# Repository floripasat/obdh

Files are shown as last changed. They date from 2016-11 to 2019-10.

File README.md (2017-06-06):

# OBDH
On-Board Data Handling module of the FloripaSat Cubesat Project

The main goal of On Board Data Handling, a.k.a. OBDH, is manage all the cubesat information aimming to reach the mission goal.

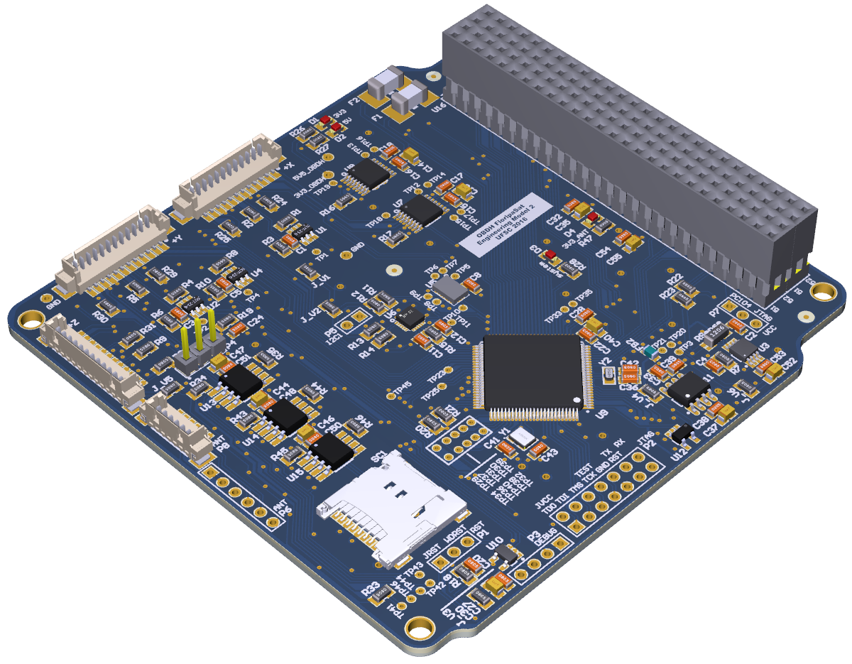
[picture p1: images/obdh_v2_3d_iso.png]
OBDH 3D ISO

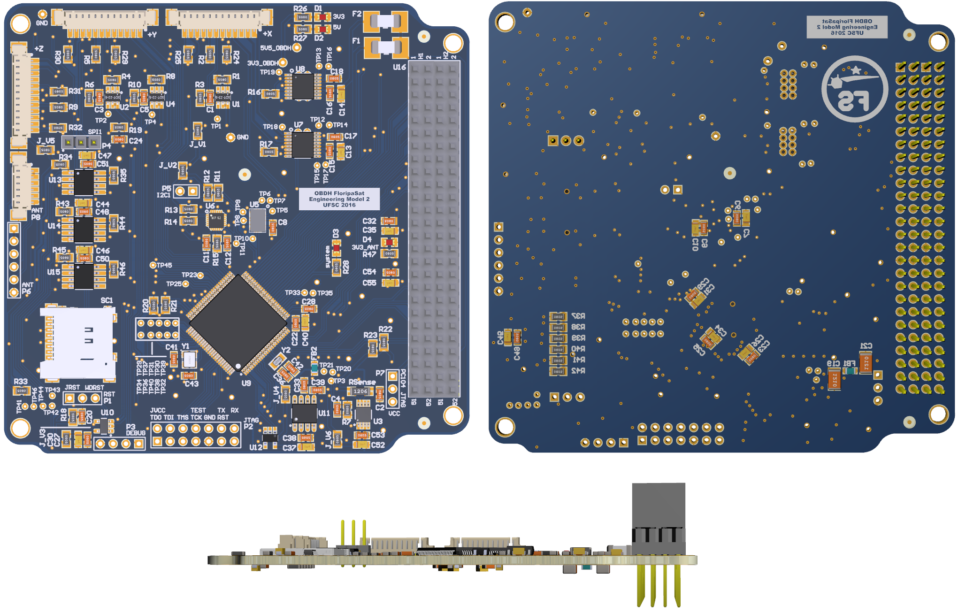
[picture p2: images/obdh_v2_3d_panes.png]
OBDH 3D Panes


## Hardware

* The MCU used in this module is the [MSP430F6659](http://www.ti.com/product/MSP430F6659);
* The tracking IC used is [MPU9250](https://www.invensense.com/products/motion-tracking/9-axis/mpu-9250/), which contains a 9-axis sensors (3-axis each): a gyroscope, an accelerometer and a compass;
* For space-ground communications, is used the radio transceiver [CC1125](http://www.ti.com/product/CC1125);
* Detailed information can be found [here](https://github.com/floripasat/obdh/hardware/).

## Software

* The programming language is C;
* All software was developed in the [Code Composer Studio IDE](http://www.ti.com/tool/ccstudio).
* Tested in compiler TI v16.9.1 LTS (CCS v7.1 7.1.0.00015).
* Uses FreeRTOS, a RTOS for embedded systems. [FreeRTOS page](http://freertos.org/);
* Detailed information can be found [here](https://github.com/floripasat/obdh/firmware/).
<!-- * Doxygen documentation [here](http://fsat-server.duckdns.org:8000/obdh/). nao foi feito ainda -->

### Toolchain setup
* Download and install Code Composer Studio: http://processors.wiki.ti.com/index.php/Download_CCS
* Instructions for for Linux enviroment: http://processors.wiki.ti.com/index.php/Linux_Host_Support_CCSv7
* Select package: MSP430 Ultra Low Power MCUs 
* After installed, open and update CCSv7: Help->Check for Updates->Select All-> Update.. / Restart
* Get the source code: `git clone https://github.com/floripasat/obdh`
* Add the project compiler version: CCS->Help->Install New Software->Work with: All available sites->Disable 'Show only latest version'->Check TI Compoler Updates: MSP430 Compiler Tools 16.6.0 ->Finish/Install/Restart
* Import source project into CCSv7: File->Import->Code Composer Studio->CCS Projects; Select the source folder: obdh/firmware; Leave 'Copy projects into workspace' unchecked.
## References

The general documentation of the project can be found in [GitBook](https://www.gitbook.com/book/tuliogomesp/floripasat-technical-manual).

All source code of the project can be found in [GitHub](https://github.com/floripasat).

The official website of the project is [www.floripasat.ufsc.br](http://www.floripasat.ufsc.br/).

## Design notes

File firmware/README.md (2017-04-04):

# FloripaSat - On Board Data Handling - Software

## FreeRTOS

* Language: C
* The MCU used in this module is the [MSP430F6659](http://www.ti.com/product/MSP430F6659).
* As transceiver, the [CC1125](http://www.ti.com/product/CC1125) IC is used.
* All MCU peripherals are controlled with the ["MSP Driver Library"](http://www.ti.com/tool/mspdriverlib) library, also know as ["DriverLib"](http://www.ti.com/tool/mspdriverlib).
* All software was developed in the [Code Composer Studio IDE](http://www.ti.com/tool/ccstudio) (version 7.1.0.00015), a.k.a. CCS. The compiler used is TI MSP430 Compiler, version 16.9.1 LTS).

## Software flow

1. Antenna Deployment Countdown 
2. Antenna Deployment
3. Watchdog timer configuration
4. Peripherals initialization 
5. Start tasks

## USCI Configuration

| MSP INTERFACE | MODE | CONNECTED COMPONENTS |
|:---|:---|:---|
| USCI_A0 | SPI | TRANSCEIVER |
| USCI_A1 | SPI | MAIN BUS (flash/SD memory, ADC1, ADC2, ADC3, ADCS) |
| USCI_A2 | UART | DEBUG |
| USCI_B0 | I2C | EPS (EPS as slave) |
| USCI_B1 | I2C | MAIN BUS (IMU1, IMU2) |
| USCI_B2 | I2C | ANTENNA DEPLOYMENT |

## Debug mode

The Debug mode was used to print log messages.

The debug mode can be used with a UART-USB converter (FTDI chip for example) with the follow configuration:
* Baudrate = 9600 bps
* Data bits = 8
* Parity bit = None
* Stop bits = 1

## References

The general documentation of the project can be found in [GitBook](https://www.gitbook.com/book/tuliogomesp/floripasat-technical-manual).

All source code of the project can be found in [GitHub](https://github.com/floripasat/).

The official website of the project is [www.floripasat.ufsc.br](http://www.floripasat.ufsc.br/).

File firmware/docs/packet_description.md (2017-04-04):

# Packet Description

Esse documento deve seguir as informações contidas em: https://docs.google.com/spreadsheets/d/1e5KTyQqeFW5pgzqara0UhxRcPHhF5Oq5QgL1BtvwexI

## Package flags

### Length (bytes)
2

### Description

Contém 1 bit flag para cada um dos submódulos seguintes do pacote. Se o bit estiver setado, significa que o pacote contém dados daquele determinado módulo. Durante a persistência de dados em memória não-volátil, uma flag zerada significa que os dados do submódulo referido serão armazenados com o valor 0 e podem ser ignorados no pacote, porém mantendo o pacote de tamanho fixo. Já durante um envio de dados para o segmento terrestre, uma flag zerada significa que o pacote não contém aquela seção de dados referente ao submódulo, fazendo com que o tamanho total do pacote seja menor.

## System status

### Length (bytes)
5

### Description

Contém um contador de resets (3 bytes) e flags que sinalizam quais submódulos estão funcionando (2 bytes). 

## IMU

### Length (bytes)
20

### Description
Inercial Measure Unit data.

3-axis accelerometer - 6 bytes
<p><strong>Cálculo:</strong>   (((HIGH_BYTE << 8 | LOW_BYTE) * IMU_ACC_RANGE) / 32768.0) , onde IMU_ACC_RANGE depende da sensibilidade configurada (2g a 16g).</p>

3-axis gyroscope - 6 bytes
<p><strong>Cálculo:</strong>   (((HIGH_BYTE << 8 | LOW_BYTE) * IMU_GYRO_RANGE) / 32768.0) , onde IMU_GYRO_RANGE depende da sensibilidade configurada (250º/s a 2000º/s).</p>

3-axis magnetometer - 6 bytes

temperature - 2 bytes

<p><strong>Cálculo:</strong>   (((HIGH_BYTE << 8 | LOW_BYTE) / IMU_TEMP_RANGE ) + 21), onde IMU_TEMP_RANGE = 500.</p>

## MSP Sensors

### Length (bytes)
6
### Description

MSP internal temperature sensor (2 bytes)

<p><strong>Cálculo:</strong>   ((HIGH_BYTE << 8 | LOW_BYTE) * 2 - COEF_30C) * 55) / (COEF_85C - COEF_30C) + 30, onde COEF_XX é o coeficiente de calibraçao salvo na memoria flash do MSP.</p>

Supply voltage (2 bytes)

<p><strong>Cálculo:</strong>    (HIGH_BYTE << 8 | LOW_BYTE) * AVCC * VOLTAGE_DIVISOR / ADC_RANGE, onde AVCC = 3.3, VOLTAGE_DIVISOR = 2, ADC_RANGE = 3.</p>

Supply current (2 bytes)
<p><strong>Cálculo:</strong>    (HIGH_BYTE << 8 | LOW_BYTE) * (AVCC / (ADC_RANGE * RL_VALUE * CURRENT_GAIN * RSENSE_VALUE), onde AVCC = 3.3, ADC_RANGE = 3, RL_VALUE = 0.05, CURRENT_GAIN = 0.025 e RSENSE_VALUE = 20000.</p>

## Systick

### Length (bytes)
4

### Description
Tempo desde o último reset, em milisegundos.

## Solar Panels

### Length (bytes)
42

### Description
3 solar panels has 1-axis accelerometer, gyroscope and magnetometer (2 bytes each axis each panel). Every panels has a sun sensor and a temperature sensor (2 bytes each). (2+2+2) * 3 + (2+2) * 6 = 42 bytes.

## RTC

### Length (bytes)
8

### Description
Seconds, minutes, hours, day of week, day of month, month (1 byte each) and year (2 bytes).

## Radio

### Length (bytes)
100

### Description
RSSI do rádio (2 bytes)
Últimos comandos recebidos

## ADC Solar Panels

### Length (bytes)
18

### Description
ADC solar panel current - 12 bytes
ADC solar panel voltage - 6 bytes

## MSP430 ADC

### Length (bytes)
8

### Description
ADC total voltage - 2 bytes 
ADC bus voltage - 2 bytes
ADC beacon/eps current - 2 bytes
ADC internal temperature sensor - 2 bytes

## Battery Monitor

### Length (bytes)
21

### Description
Battery average current - 2 bytes
Battery monitor temperature - 2 bytes
Battery voltage - 4 bytes
Battery current - 2 bytes
Battery accumulated current - 2 bytes
Protection register - 1 byte
Status register - 1 byte
Cycle counter register - 1 byte
Remaining active absolute capacity register - 2 bytes
Remaining standby absolute capacity register - 2 bytes
Remaining active relative capacity - 1 byte
Remaining standby relative capacity - 1 byte

## ADS1248

### Length (bytes)
21

### Description
7 RTDs measurements via ADS1248 - 21 bytes

## Task Scheduler

### Length (bytes)
1

### Description
EPS status - 1 byte

## Beacon

### Length (bytes)
3

### Description
Radio temperature - 1 byte
Transmitted power - 1 byte
DAC voltage (power amplifier control) - 1 byte

## Transceiver

### Length (bytes)
4

### Description
Radio temperature - 1 byte
Received signal power - 1 byte
Transmitted power - 1 byte
DAC voltage (power amplifier control) - 1 byte

## Payload1

### Length (bytes)
7

### Description
Voltage on the thermoeletric generator with/without load and energy stored on the last 3 minutes (7 bytes total)

## Payload2

### Length (bytes)
100

### Description
Single Event Upset Detection

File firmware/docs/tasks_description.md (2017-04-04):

# Tasks Description

## wdt_task

#### Descrição

Esta tarefa irá resetar os dois watchdog timers (interno e externo) a cada execução. No modo DEBUG ela também faz o system_led piscar para termos um recurso visual no momento da depuração.

#### Dados gerados

Nenhum

#### Período da tarefa

500 ms.

#### Prioridade

5

#### Recursos utilizados

GPIO WDI_EXT;
GPIO LED_SYSTEM.

## store_data_task

#### Descrição

Esta tarefa recebe, por meio de filas de mensagens, os dados de outras tarefas, os quais deve salvar em uma memória não-volátil. Os dados são salvos em blocos de 512 bytes. Os dados são armazenados conforme a tabela: https://docs.google.com/spreadsheets/d/1e5KTyQqeFW5pgzqara0UhxRcPHhF5Oq5QgL1BtvwexI. 

O esquema de armazenamento dá-se da seguinte forma: se houver mensagens (novos dados) na fila de mensagens referente a determinado submódulo, sua respectiva flag é setada no pacote e os dados salvos na memória. Os submódulos que não possuírem novas mensagens são zerados no pacote, juntamente com sua flag, e ambos salvos na memória (com valor 0). No momento da leitura do pacotes salvos em memória, as flags irão indicar quais submódulos contém dados válidos e quais devem ser ignorados. Isso faz com que as transmissões de dados enviem somente informações relevantes, economizando banda de transmissão.

#### Dados gerados

Não se aplica

#### Período da tarefa

Depende das demais tarefas: ela deve ter período menor ou igual ao menor período das outras tarefas, de maneira a não perder nenhuma leitura.

#### Prioridade

5

#### Recursos utilizados

GPIO uSDCard_CE;
GPIO Mem_WP;
GPIO Mem0_CE;
GPIO Mem1_CE;
GPIO Mem2_CE;
GPIO Mem2_CE;
GPIO Mem2_CE;
SPI 1 (USCI A1).

## communications_task

#### Descrição

Esta tarefa controla o Link de comunicação (uplink e downlink). Ela irá aguardar a recpeção de mensagens pelo rádio (uplink) e, eventualmente, responderá aos comandos recebidos. Alguns comandos são:
- Shutdown all communications over 24 hours;
- Send data (com as especificações dos dados desejados).

#### Dados gerados

RSSI do rádio
Últimos comandos recebidos

#### Período da tarefa

100ms

#### Prioridade

5

#### Recursos utilizados

GPIO TTC_GPIO0_MAIN;
GPIO TTC_GPIO2_MAIN;
GPIO TTC_RESETn_MAIN;
GPIO TTC_CTRL_RF_SWT_TX;
GPIO TTC_CTRL_RF_SWT_RX;
GPIO Mem2_CE;
GPIO Mem2_CE;
SPI 0 (USCI A0);
GPIO uC_BEACON_0;
GPIO uC_BEACON_1;
GPIO uC_BEACON_2;
GPIO uC_BEACON_3.

## read_internal_sensors_task

#### Descrição

Esta tarefa faz a leitura do sensor de temperatura interno do MSP, da tensão e da corrente de alimentação. Estes valores são enviados por meio de uma fila de mensagens para a tarefa store_data.

#### Dados gerados

Internal temperature (2 bytes)
Supply voltage (2 bytes)
Supply current (2 bytes)
TOTAL = 6 bytes

#### Período da tarefa

1000ms

#### Prioridade

1

#### Recursos utilizados

GPIO OBDH_CURRENT_ADC;
GPIO ADC_VCC_3V3;
ADC.

## imu_interface_task

#### Descrição

Esta tarefa faz a leitura dos sensores que compõem a IMU (Inertial Measure Unit). Estes são: acelerômetro, giroscópio e magnetômetro, em 3 eixos, e um sensor de temperatura. 

#### Dados gerados

Accelerometer axis X(2 bytes)
Accelerometer axis Y(2 bytes)
Accelerometer axis Z(2 bytes)
Gyroscope axis X(2 bytes)
Gyroscope axis Y(2 bytes)
Gyroscope axis Z(2 bytes)
Magnetometer axis X(2 bytes)
Magnetometer axis Y(2 bytes)
Magnetometer axis Z(2 bytes)
Temperature sensor(2 bytes)
TOTAL = 20 bytes

#### Período da tarefa

10.000ms

#### Prioridade

1

#### Recursos utilizados

I2C 1.

## debug_task

#### Descrição

Esta tarefa somente é criada quando o build está em modo "DEBUG". Ela imprime mensagens, via UART, 

#### Dados gerados

Internal temperature (2 bytes)
Supply voltage (2 bytes)
Supply current (2 bytes)
TOTAL = 6 bytes

#### Período da tarefa

1000ms

#### Prioridade

1

#### Recursos utilizados

GPIO OBDH_CURRENT_ADC;
GPIO ADC_VCC_3V3;
ADC.

## imu_interface_task

#### Descrição

Esta tarefa faz a leitura dos sensores que compõem a IMU (Inertial Measure Unit). Estes são: acelerômetro, giroscópio e magnetômetro, em 3 eixos, e um sensor de temperatura. 

#### Dados gerados

Accelerometer axis X(2 bytes)
Accelerometer axis Y(2 bytes)
Accelerometer axis Z(2 bytes)
Gyroscope axis X(2 bytes)
Gyroscope axis Y(2 bytes)
Gyroscope axis Z(2 bytes)
Magnetometer axis X(2 bytes)
Magnetometer axis Y(2 bytes)
Magnetometer axis Z(2 bytes)
Temperature sensor(2 bytes)
TOTAL = 20 bytes

#### Período da tarefa

10.000ms

#### Prioridade

1

#### Recursos utilizados

I2C 1.

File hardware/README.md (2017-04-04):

# FloripaSat - On Board Data Handling - Hardware
<hr>
## Topology

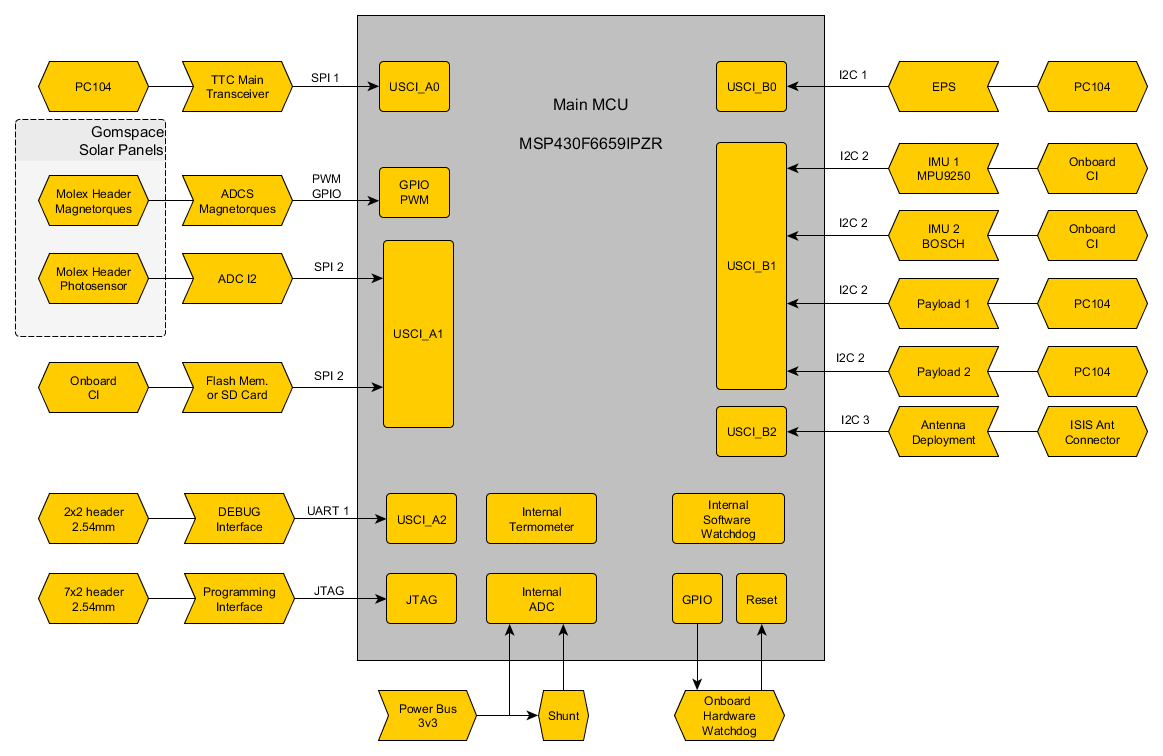
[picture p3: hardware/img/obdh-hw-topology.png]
Topology
  

<hr>

## Pin Assignaments

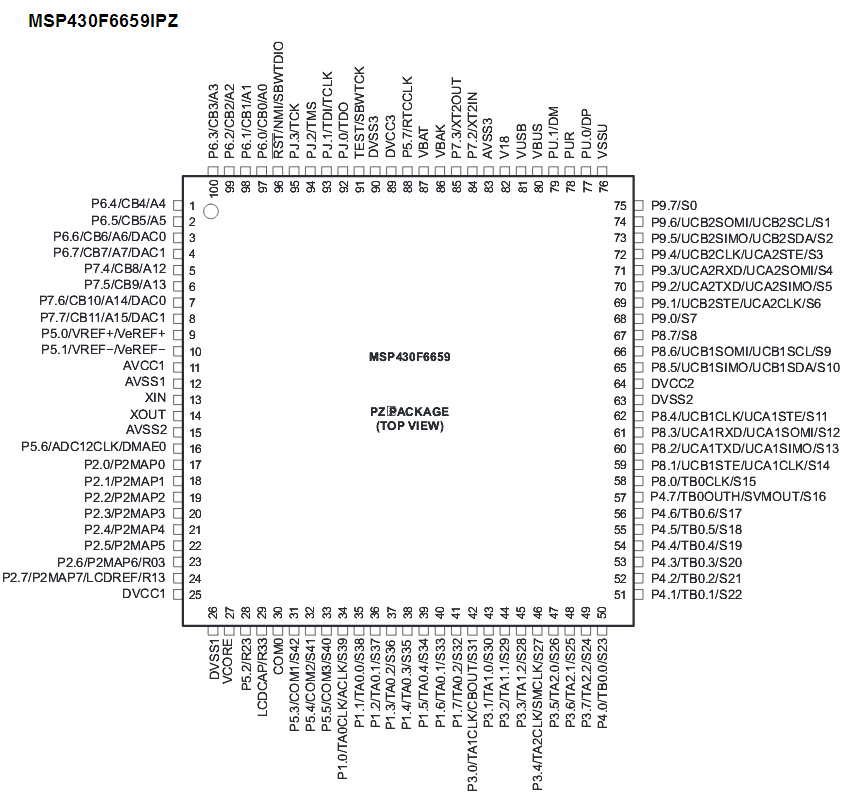
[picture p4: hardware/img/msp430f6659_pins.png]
Pin Designation
  

| PIN  NUMBER | PIN  NAME | OBDH  NAME |
|:--|:---|:---|
|1  |P6.4/CB4/A4 ||
|2  |P6.5/CB5/A5 ||
|3  |P6.6/CB6/A6/DAC0 ||
|4  |P6.7/CB7/A7/DAC1 ||
|5  |P7.4/CB8/A12 ||
|6  |P7.5/CB9/A13 ||
|7  |P7.6/CB10/A14/DAC0 ||
|8  |P7.7/CB11/A15/DAC1 ||
|9  |P5.0/VREF+/VeREF+ ||
|10 |P5.1/VREF-/VeREF- ||
|11 |AVCC1 ||
|12 |AVSS1 ||
|13 |XIN ||
|14 |XOUT ||
|15 |AVSS2 ||
|16 |P5.6/ADC12CLK/DMAE0 ||
|17 |P2.0/P2MAP0 ||
|18 |P2.1/P2MAP1 ||
|19 |P2.2/P2MAP2 ||
|20 |P2.3/P2MAP3 ||
|21 |P2.4/P2MAP4 ||
|22 |P2.5/P2MAP5 ||
|23 |P2.6/P2MAP6/R03 ||
|24 |P2.7/P2MAP7/LCDREF/R13 ||
|25 |DVCC1 ||
|26 |DVSS1 ||
|27 |VCORE ||
|28 |P5.2/R23 ||
|29 |LCDCAP/R33 ||
|30 |COM0 ||
|31 |P5.3/COM1/S42 ||
|32 |P5.4/COM2/S41 ||
|33 |P5.5/COM3/S40 ||
|34 |P1.0/TA0CLK/ACLK/S39 ||
|35 |P1.1/TA0.0/S38 ||
|36 |P1.2/TA0.1/S37 ||
|37 |P1.3/TA0.2/S36 ||
|38 |P1.4/TA0.3/S35 ||
|39 |P1.5/TA0.4/S34 ||
|40 |P1.6/TA0.1/S33 ||
|41 |P1.7/TA0.2/S32 ||
|42 |P3.0/TA1CLK/CBOUT/S31 ||
|43 |P3.1/TA1.0/S30 ||
|44 |P3.2/TA1.1/S29 ||
|45 |P3.3/TA1.2/S28 ||
|46 |P3.4/TA2CLK/SMCLK/S27 ||
|47 |P3.5/TA2.0/S26 ||
|48 |P3.6/TA2.1/S25 ||
|49 |P3.7/TA2.2/S24 ||
|50 |P4.0/TB0.0/S23 ||
|51 |P4.1/TB0.1/S22 ||
|52 |P4.2/TB0.2/S21 ||
|53 |P4.3/TB0.3/S20 ||
|54 |P4.4/TB0.4/S19 ||
|55 |P4.5/TB0.5/S18 ||
|56 |P4.6/TB0.6/S17 ||
|57 |P4.7/TB0OUTH/SVMOUT/S16  ||
|58 |P8.0/TB0CLK/S15 ||
|59 |P8.1/UCB1STE/UCA1CLK/S14 ||
|60 |P8.2/UCA1TXD/UCA1SIMO/S13||
|61 |P8.3/UCA1RXD/UCA1SOMI/S12||
|62 |P8.4/UCB1CLK/UCA1STE/S11 ||
|63 |DVSS2 ||
|64 |DVCC2 ||
|65 |P8.5/UCB1SIMO/UCB1SDA/S10||
|66 |P8.6/UCB1SOMI/UCB1SCL/S9 ||
|67 |P8.7/S8 ||
|68 |P9.0/S7 ||
|69 |P9.1/UCB2STE/UCA2CLK/S6  ||
|70 |P9.2/UCA2TXD/UCA2SIMO/S5 ||
|71 |P9.3/UCA2RXD/UCA2SOMI/S4 ||
|72 |P9.4/UCB2CLK/UCA2STE/S3  ||
|73 |P9.5/UCB2SIMO/UCB2SDA/S2 ||
|74 |P9.6/UCB2SOMI/UCB2SCL/S1 ||
|75 |P9.7/S0 ||
|76 |VSSU ||
|77 |PU.0/DP ||
|78 |PUR ||
|79 |PU.1/DM ||
|80 |LDOI ||
|81 |VUSB ||
|82 |V18 ||
|83 |AVSS3 ||
|84 |P7.2/XT2IN ||
|85 |P7.3/XT2OUT ||
|86 |VBAK ||
|87 |VBAT ||
|88 |P5.7/RTCCLK ||
|89 |DVCC3 ||
|90 |DVSS3 ||
|91 |TEST/SBWTCK ||
|92 |PJ.0/TDO ||
|93 |PJ.1/TDI/TCLK ||
|94 |PJ.2/TMS ||
|95 |PJ.3/TCK ||
|96 |RST/NMI/SBWTDIO ||
|97 |P6.0/CB0/A0 ||
|98 |P6.1/CB1/A1 ||
|99 |P6.2/CB2/A2 ||
|100|P6.3/CB3/A3 ||
<hr>

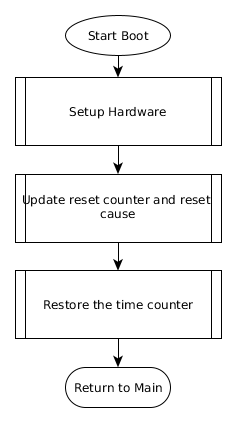
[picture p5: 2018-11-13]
images/flowcharts/boot_flowchart.png

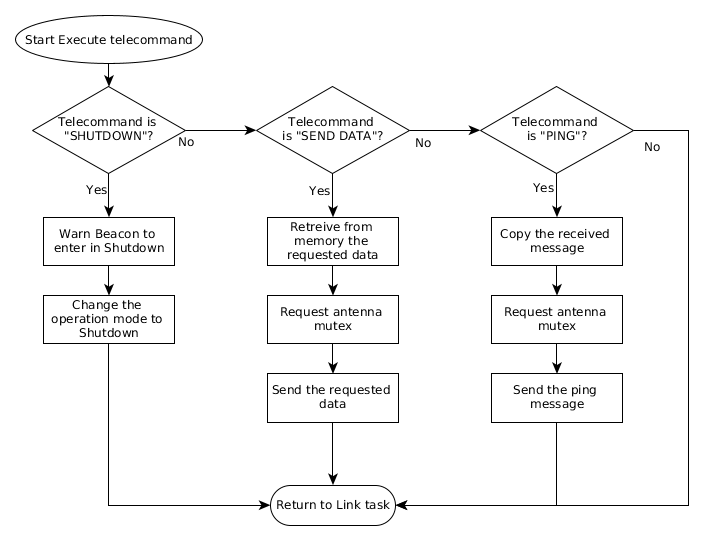
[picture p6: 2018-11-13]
images/flowcharts/execute_telecommand_flowchart.png

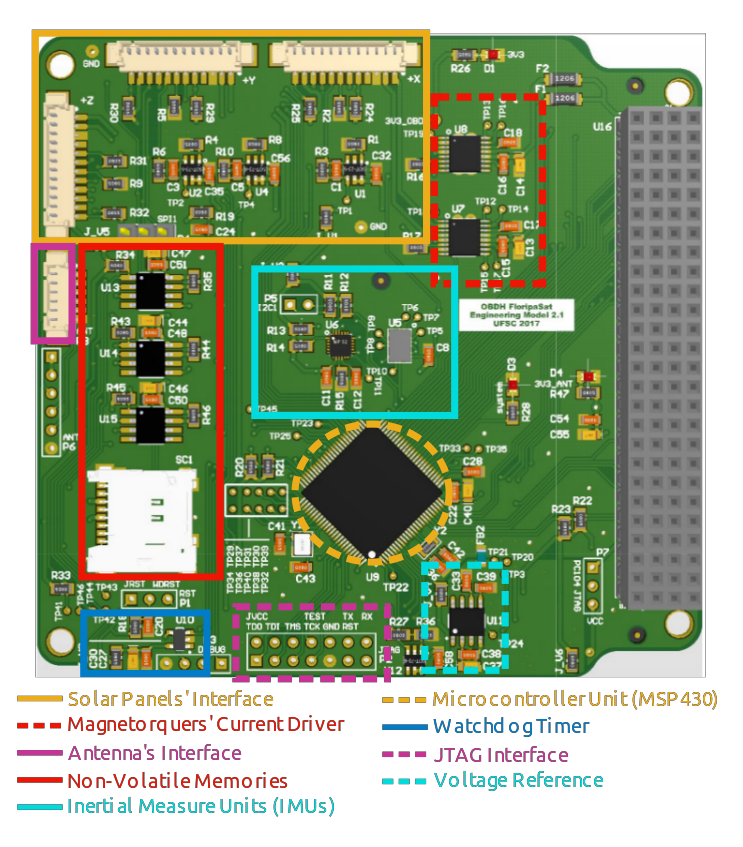
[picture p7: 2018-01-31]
images/obdh-hw-submodules.png

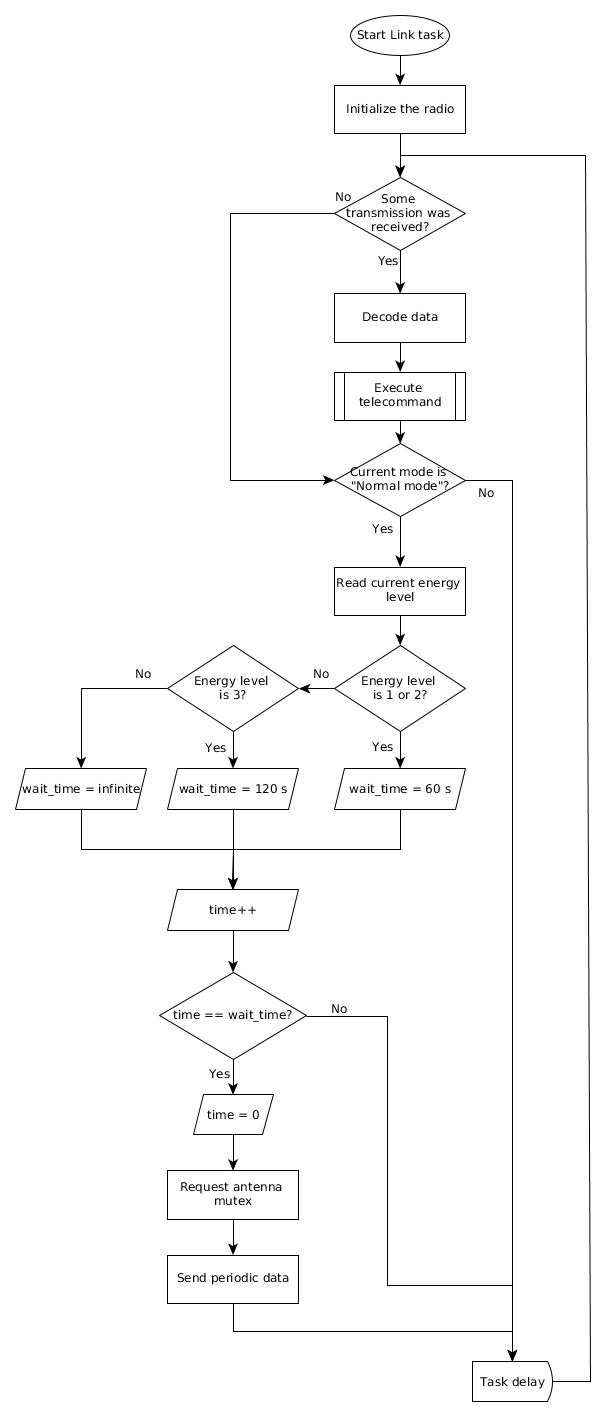
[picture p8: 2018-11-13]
images/flowcharts/link_task_flowchart.png

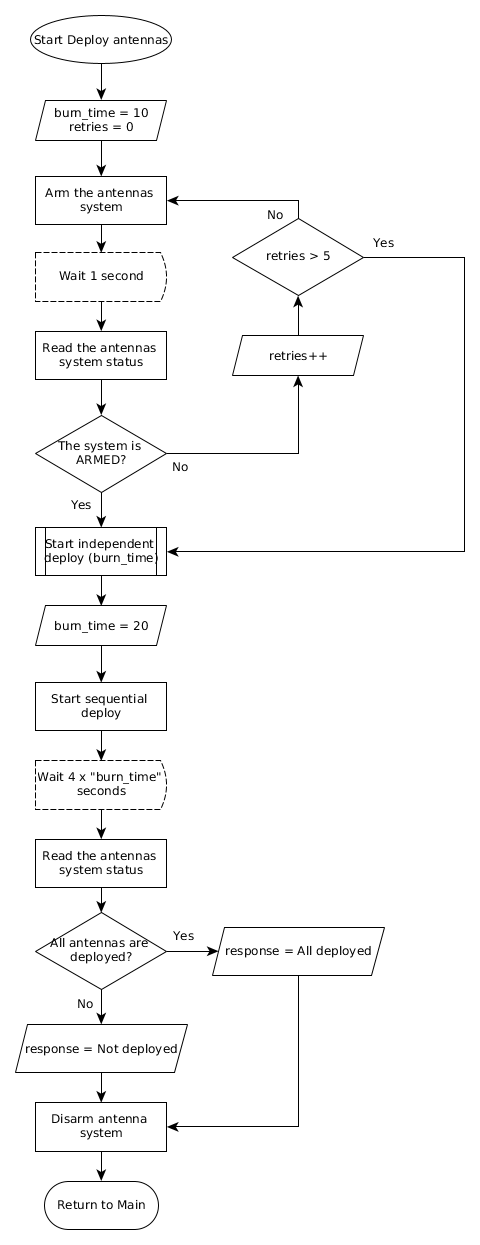
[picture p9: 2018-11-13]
images/flowcharts/deploy_antennas_flowchart.png

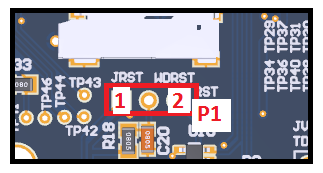
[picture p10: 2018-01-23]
images/obdh_jumper_reset_source.png

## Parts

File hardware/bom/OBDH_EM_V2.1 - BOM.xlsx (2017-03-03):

Mount | Designator | Manufacter PartNumber | Digikey Part Number | Description | Qtd | Price per unit(USD) | Total
TRUE | C13, C14 | TPSP106M010R2000 | 511-1685-1-ND (http://www.digikey.com/product-detail/en/rohm-semiconductor/TCP1A106M8R/511-1685-1-ND/4571361) | 10µF Molded Tantalum Capacitors 10V | 2 | $0.60 | $1.20
TRUE | C7, C10, C26, C30, C31, C34, C37, C40, C44, C45, C46, C47, C52, C55 | F920J106MPA | 478-8115-1-ND (http://www.digikey.com/product-detail/en/avx-corporation/F920J106MPA/478-8115-1-ND/4005541) | 10µF Molded Tantalum Cap 6.3V 0805 | 14 | $0.22 | $3.05
TRUE | C17, C18 | C2012X7R1C225K125AB | 445-1420-1-ND (http://www.digikey.com/product-detail/en/tdk-corporation/C2012X7R1C225K125AB/445-1420-1-ND/569086) | 2.2µF 16V Ceramic Capacitor X7R 0805 | 2 | $0.20 | $0.40
TRUE | C19, C21 | C3225X7R1C226K250AC | 445-3945-1-ND (http://www.digikey.com/product-detail/en/tdk-corporation/C3225X7R1C226K250AC/445-3945-1-ND/1944441) | 22µF 16V Ceramic Capacitor X7R 1210 | 2 | $0.85 | $1.70
TRUE | C36, C42 | CL21C120FBANNNC | 1276-2579-1-ND (http://www.digikey.com/product-detail/en/samsung-electro-mechanics-america-inc/CL21C120FBANNNC/1276-2579-1-ND/3890665) | 12pF 50V Ceramic Capacitor C0G, NP0 0805 | 2 | $0.13 | $0.26
TRUE | C11, C15, C16, C39 | CL21B103KAANNNC | 1276-2434-1-ND (http://www.digikey.com/product-detail/en/samsung-electro-mechanics-america-inc/CL21B103KAANNNC/1276-2434-1-ND/3890520) | CAP CER 0.01uF 25V 10% X7R 0805 | 4 | $0.10 | $0.40
TRUE | C28 | C0805C474K5RACTU | 399-8100-1-ND (http://www.digikey.com/product-detail/en/kemet/C0805C474K5RACTU/399-8100-1-ND/3471823) | 0.47µF 50V Ceramic Capacitor X7R 0805 | 1 | $0.25 | $0.25
FALSE | C24 | CGA4J2C0G1H223J125AA | 445-6949-1-ND (http://www.digikey.com/product-detail/en/tdk-corporation/CGA4J2C0G1H223J125AA/445-6949-1-ND/2672967) | 0.022µF ±5% 50V Ceramic Capacitor C0G, NP0 0805 | 1 | $0.32 | $0.32
TRUE | C20 | C0805C473J3GACTU | 399-8092-1-ND (http://www.digikey.com/product-detail/en/kemet/C0805C473J3GACTU/399-8092-1-ND/3471815) | 0.047µF 25V Ceramic Capacitor C0G, NP0 0805 | 1 | $0.72 | $0.72
TRUE | C1, C3, C5 | CC0805JRNPO9BN180 | 311-1102-1-ND (http://www.digikey.com/product-detail/en/yageo/CC0805JRNPO9BN180/311-1102-1-ND/303012) | 18pF 50V Ceramic Capacitor C0G, NP0 0805 | 3 | $0.10 | $0.30
TRUE | C2, C4, C6, C8, C9, C12, C22, C23, C25, C27, C29, C32, C33, C35, C38, C48, C49, C50, C51, C53, C54, C56, C58 | CC0805KRX7R8BB104 | 311-1141-1-ND (http://www.digikey.com/product-detail/en/yageo/CC0805KRX7R8BB104/311-1141-1-ND/303051) | CAP CER 0.1UF 25V 10% X7R 0805 | 23 | $0.05 | $1.15
FALSE | C41, C43 | 08051A100FAT2A | 478-5779-1-ND (http://www.digikey.com/product-detail/en/avx-corporation/08051A100FAT2A/478-5779-1-ND/2136371) | 10pF 100V Ceramic Capacitor C0G, NP0 0805 | 2 | $0.46 | $0.92
TRUE | J_V1, J_V2, J_V3, J_V4, J_V5, J_V6, R1, R2, R4, R5, R8, R9, R13, R14, R15 | RC0805JR-070RL | 311-0.0ARCT-ND (http://www.digikey.com/product-detail/en/yageo/RC0805JR-070RL/311-0.0ARCT-ND/731163) | RES SMD 0.0 OHM JUMPER 1/8W 0805 | 17 | $0.02 | $0.31
TRUE | R11, R12, R20, R21, R22, R23, R24, R25, R29, R30, R31, R32, R33, R34, R35, R43, R44, R45, R46 | CRCW080510K0FKEA | 541-10.0KCCT-ND (http://www.digikey.com/product-detail/en/vishay-dale/CRCW080510K0FKEA/541-10.0KCCT-ND/1180897) | RES 10K OHM 1/8W 1% 0805 | 19 | $0.04 | $0.76
FALSE | R37, R38, R39, R40, R41, R42 | CRCW080510K0FKEA | 541-10.0KCCT-ND (http://www.digikey.com/product-detail/en/vishay-dale/CRCW080510K0FKEA/541-10.0KCCT-ND/1180897) | RES 10K OHM 1/8W 1% 0805 | 6 | $0.04 | $0.24
TRUE | R7 | PCF0805R-1K65BT1 | 985-1304-1-ND (http://www.digikey.com/product-detail/en/tt-electronics-welwyn/PCF0805R-1K65BT1/985-1304-1-ND/2402146) | RES SMD 1.65KOHM 0.1% 1/10W 0805 | 1 | $0.61 | $0.61
TRUE | R18, R27, R36 | RC0805FR-0747KL | 311-47.0KCRCT-ND (http://www.digikey.com/product-detail/en/yageo/RC0805FR-0747KL/311-47.0KCRCT-ND/730920) | RES SMD 47K OHM 1% 1/8W 0805 | 1 | $0.01 | $0.01
FALSE | R19 | RC0805FR-0733KL | 311-33.0KCRCT-ND (http://www.digikey.com/product-detail/en/yageo/RC0805FR-0733KL/311-33.0KCRCT-ND/730810) | RES SMD 33K OHM 1% 1/8W 0805 | 1 | $0.01 | $0.01
TRUE | R16, R17 | RL1220S-R20-F | RL12S.20FCT-ND (http://www.digikey.com/product-detail/en/susumu/RL1220S-R20-F/RL12S.20FCT-ND/433023) | RES SMD 0.2 OHM 1% 1/3W 0805 | 2 | $0.32 | $0.64
TRUE | R26, R47 | RC0805FR-071KL | 311-1.00KCRCT-ND (http://www.digikey.com/product-detail/en/yageo/RC0805FR-071KL/311-1.00KCRCT-ND/730391) | RES SMD 1K OHM 1% 1/8W 0805 | 2 | $0.01 | $0.02
TRUE | R28 | RC0805FR-07330RL | 311-330CRCT-ND (http://www.digikey.com/product-detail/en/yageo/RC0805FR-07330RL/311-330CRCT-ND/730813) | RES SMD 330 OHM 1% 1/8W 0805 | 1 | $0.01 | $0.01
TRUE | R3, R6, R10 | RC0805FR-073K3L | 311-3.30KCRCT-ND (http://www.digikey.com/product-detail/en/yageo/RC0805FR-073K3L/311-3.30KCRCT-ND/730760) | RES SMD 3.3K OHM 1% 1/8W 0805 | 3 | $0.01 | $0.03
TRUE | RSense | LVK12R050DER | LVK12R050DERCT-ND (http://www.digikey.com/product-detail/en/ohmite/LVK12R050DER/LVK12R050DERCT-ND/1632800) | RES SMD 0.05 OHM 0.5% 1/2W 1206 | 1 | $0.86 | $0.86
TRUE | Y2 | ECS-.327-12.5-34S-TR | XC1967CT-ND (http://www.digikey.com/product-detail/en/ecs-inc/ECS-.327-12.5-34S-TR/XC1967CT-ND/3927391) | 32.768kHz ±20ppm Crystal 12.5pF 70 kOhm -40°C ~ 125°C Surface Mount 2-SMD | 1 | $1.20 | $1.20
TRUE | Y1 | ABM8X-102-32.000MHZ-T | 535-11454-1-ND (http://www.digikey.com/product-detail/en/abracon-llc/ABM8X-102-32.000MHZ-T/535-11454-1-ND/2673402) | 32MHz ±10ppm Crystal 10pF 60 Ohm -40°C ~ 125°C Surface Mount 4-SMD | 1 | $6.18 | $6.18
TRUE | D1, D4 | LTST-C171GKT | 160-1423-1-ND (http://www.digikey.com/product-detail/en/lite-on-inc/LTST-C171GKT/160-1423-1-ND/386792) | Green 569nm LED Indication - Discrete 2.1V 0805 (2012 Metric) | 1 | $0.29 | $0.29
TRUE | D3 | LTST-C170KFKT | 160-1413-1-ND (http://www.digikey.com/product-detail/en/lite-on-inc/LTST-C170KFKT/160-1413-1-ND/386774) | Orange 605nm LED Indication - Discrete 2V 0805 (2012 Metric) | 1 | $0.29 | $0.29
TRUE | F1, F2 | 0437.375WR | F2878CT-ND (http://www.digikey.com/product-detail/en/littelfuse-inc/0437.375WR/F2878CT-ND/1905893) | FUSE BOARD MNT 375MA 125VAC/VDC | 2 | $0.96 | $1.92
TRUE | FB1, FB2 | BLM21PG300SN1D | 490-1052-1-ND (http://www.digikey.com/product-detail/en/murata-electronics-north-america/BLM21PG300SN1D/490-1052-1-ND/584499) | FERRITE BEAD 30 OHM 0805 1LN | 2 | $0.12 | $0.24
TRUE | U6 | MPU-9250 | 1428-1019-1-ND (http://www.digikey.com/product-search/en?keywords=1428-1019-1-ND) | GYRO/ACCEL/COMPASS/9-AXIS | 1 | $10.64 | $10.64
TRUE | U5 | BMX055 | 828-1060-1-ND (http://www.digikey.com/product-detail/en/bosch-sensortec/BMX055/828-1060-1-ND/6136311) | Bosch Adx/Gyro/Magneto 3 axis | 1 | $7.99 | $7.99
TRUE | U1, U2, U4, U12 | TLV341AIDBVR | 296-17680-1-ND (http://www.digikey.com/product-detail/en/texas-instruments/TLV341AIDBVR/296-17680-1-ND/716532) | General Purpose Amplifier 1 Circuit Rail-to-Rail SOT-23-6 | 4 | $1.09 | $4.36
TRUE | U13, U14, U15 | IS25LP128-JBLE | 706-1341-ND (http://www.digikey.com/product-detail/en/issi-integrated-silicon-solution-inc/IS25LP128-JBLE/706-1341-ND/5189776) | IC FLASH 128MBIT 133MHZ 8SOIC | 3 | $2.21 | $6.63
TRUE | U7, U8 | DRV8833PWPR | 296-29434-1-ND (http://www.digikey.com/product-detail/en/texas-instruments/DRV8833PWPR/296-29434-1-ND/2743171) | IC MOTOR DRIVER PAR 16HTSSOP | 2 | $2.46 | $4.92
TRUE | U9 | MSP430F6659IPZ | 296-41521-ND (http://www.digikey.com/product-detail/en/texas-instruments/MSP430F6659IPZ/296-41521-ND/3902666) | 16-bit Microcontrollers - MCU Mixed Signal MCU | 1 | $12.25 | $12.25
TRUE | U10 | TPS3823-33QDBVRQ1 | 296-15650-1-ND (http://www.digikey.com/product-detail/en/texas-instruments/TPS3823-33QDBVRQ1/296-15650-1-ND/2057470) | IC SUPERVISORY CIRCUIT SOT23-5 | 1 | $1.73 | $1.73
TRUE | U3 | MAX9934TAUA+ | MAX9934FAUA+-ND (http://www.digikey.com/product-detail/en/maxim-integrated/MAX9934FAUA-/MAX9934FAUA--ND/2239126) | Current Sense Amplifier 1 Circuit 8-uMAX | 1 | $1.68 | $1.68
TRUE | U11 | REF5030AQDRQ1 | 296-27911-1-ND (http://www.digikey.com/product-detail/en/texas-instruments/REF5030AQDRQ1/296-27911-1-ND/2428322) | Voltage References Low NoiseVery Low DriftPrec Vltg Ref - 3V | 1 | $3.62 | $3.62
TRUE | SC1 | 5031821852 | WM12834CT-ND (http://www.digikey.com/product-search/en?keywords=WM12834CT-ND) | 9 (8 + 1) Position Card Connector microSD™ Surface Mount, Right Angle Gold | 1 | $2.33 | $2.33
TRUE | +X, +Y, +Z | 0533981271 | WM7616CT-ND (http://www.digikey.com/product-detail/en/molex-llc/0533981271/WM7616CT-ND/699090) | 12 Positions Header, Shrouded Connector 0.049" (1.25mm) Surface Mount Tin | 3 | $2.16 | $6.48
TRUE | U16A, U16B | ESQ-126-39-G-D | SAM8772-ND (http://www.digikey.com/product-detail/en/samtec-inc/ESQ-132-39-G-D/SAM8772-ND/2640989) | CONN RCPT 64POS .100" DUAL GOLD | 2 | $11.08 | $22.16
TRUE | P1, P4, P7 | 961103-6404-AR | 3M9448-ND (http://www.digikey.com/product-detail/en/3m/961103-6404-AR/3M9448-ND/2071489) | CONN HEADER VERT SGL 3POS GOLD | 3 | $0.26 | $0.78
TRUE | P5 | M20-9990246 | 952-2262-ND (http://www.digikey.com/product-detail/en/harwin-inc/M20-9990246/952-2262-ND/3728226) | SIL VERTICAL PC TAIL PIN HEADER | 1 | $0.11 | $0.11
TRUE | P6 | 68000-406HLF | 609-3263-ND (http://www.digikey.com/product-detail/en/amphenol-fci/68000-406HLF/609-3263-ND/1878471) | CONN HEADER 6POS .100 STR TIN | 1 | $0.25 | $0.25
TRUE | P3 | 961104-6404-AR | 3M9449-ND (http://www.digikey.com/product-detail/en/3m/961104-6404-AR/3M9449-ND/2071490) | CONN HEADER VERT SGL 4POS GOLD | 1 | $0.33 | $0.33
TRUE | P2 | SBH11-PBPC-D07-ST-BK | S9170-ND (http://www.digikey.com/product-detail/en/sullins-connector-solutions/SBH11-PBPC-D07-ST-BK/S9170-ND/1990063) | CONN HEADER 2.54MM 14POS GOLD | 1 | $0.53 | $0.53
 |  |  |  |  |  | Grand Total | $111.07
 |  |  |  |  |  | Last Edition | 2017-02-17

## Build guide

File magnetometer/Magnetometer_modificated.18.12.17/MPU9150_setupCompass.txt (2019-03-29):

void MPU9150_setupCompass() {
    write_i2c(0x0A, 0x00); //PowerDownMode
    write_i2c(0x0A, 0x0F); //SelfTest
    write_i2c(0x0A, 0x00); //PowerDownMode
    write_i2c(0x24, 0x40); //Wait for Data at Slave0
    write_i2c(0x25, 0x8C); //Set i2c address at slave0 at 0x0C
    write_i2c(0x26, 0x02); //Set where reading at slave 0 starts
    write_i2c(0x27, 0x88); //set offset at start reading and enable
    write_i2c(0x28, 0x0C); //set i2c address at slv1 at 0x0C
    write_i2c(0x29, 0x0A); //Set where reading at slave 1 starts
    write_i2c(0x2A, 0x81); //Enable at set length to 1
    write_i2c(0x64, 0x01); //overvride register
    write_i2c(0x67, 0x03); //set delay rate
    write_i2c(0x01, 0x80);
    write_i2c(0x34, 0x04); //set i2c slv4 delay
    write_i2c(0x64, 0x00); //override register
    write_i2c(0x6A, 0x00); //clear usr setting
    write_i2c(0x64, 0x01); //override register
    write_i2c(0x6A, 0x20); //enable master i2c mode
    write_i2c(0x34, 0x13); //disable slv4
}
/*
int MPU9150_readSensor(int addrH, int addrL) {
    int H, L;
    H = read_i2c(addrH);
    clear();
    L = read_i2c(addrL);
    return (int) ((H << 8:sunglasses: + L);
}
*/

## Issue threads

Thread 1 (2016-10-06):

thread implementation to control watchdogs (sw and hw)

mariobaldini, 2016-10-06:
- thread priority: highest
- period: 100ms
- action: set a given GPIO to high for 10ms. (low otherwise).

eldertramontin, 2016-10-07:
- thread priority: highest                                                          -> (configMAX_PRIORITIES - 1)
- period: 100ms                                                                       -> (vTaskDelayUntil)
- action: set a given GPIO to high for 10ms. (low otherwise). -> (GIO 5.4[led pin on OBDH board] toggle with vTaskDelay)

mariobaldini, 2016-11-04:
Implemented.

Yet to be tested.

Closed 2016-11-28.

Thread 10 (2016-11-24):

[SW]  C lenguage style

mfrata, 2016-11-24:
Qual padrão de codificação que vamos usar no SW?
MISRA, NASA-C, Indian Hill, outra?

Importante decidir isso para colocar na documentação de SW

eldertramontin, 2016-11-28:
Vamos usar o NASA-C style, com modificações.
A princípio a única mudança é na utilização da "{" na mesma linha, e não na linha seguinte a chamada de função / definição de struct / etc.
Posteriormente podemos fazer mais algumas alterações. A referência do nosso estilo de codificação pode ser gerada em: http://www.rosvall.ie/cgi-bin/genCodeStd.pl
Vou atribuir esta issue para mim, deixando em aberto a tarefa de alterar o código atual para atender a esta decisão.

Closed 2017-03-08.

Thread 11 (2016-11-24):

[SW] - Analisar problema de frequencia de MCLK e SMCLK

eldertramontin, 2016-11-24:
Os sinais internos do MSP430 MCLK e SMCLK, não estão apresentando 4MHz, como era o esperado pois estes estão conectados ao cristal XT2 (de 4MHz na placa do modelo de engenharia v1).
A saída apresentada é de 1MHz, provavelmente proveniente do DCOCLK, conforme descrito na página 178 do User Guide:
"SMCLCK = XT2CLK when available, otherwise DCOCLKDI"

Closed 2016-12-05.

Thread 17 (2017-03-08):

Analyze OBDH / TTC Transceiver communication procedure

eldertramontin, 2017-03-08:
Just establish communication with the radio module (RF4463), over SPI.

mariobaldini, 2017-12-21:
Uma dica: quando se encerra a issue é bom ter um comentário: se foi feita
com sucesso, se não vai mais ser feita pq saiu do escopo, não é
tecnicamente viável, etc.

Vi q varias foram fechadas, mas vendo o projeto de fora, não tenho como
saber se a issue X foi implementado e fechada; ou simplesmente ignorada e
fechada.

É importante pro futuro caso alguém queira olhar a documentação pq entrou
no mesmo problema.

On Wed, 20 Dec 2017 at 20:38 eldertramontin <notifications@github.com>
wrote:

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

Closed 2017-12-20.

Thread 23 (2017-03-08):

Configure IMU

mfrata, 2017-03-08:
Use I2C driver to configure the imu registers to minimum range(gyroscope and accelerometer)

Closed 2017-04-04.

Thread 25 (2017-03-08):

Put the msp in hibernation

eldertramontin, 2017-03-08:
Put the msp430 in low power mode for 45 minutes, before the antenna deployment.

eldertramontin, 2017-03-08:
Make the msp430 wake up every 1 second, to reset the watchdog timers. A counter may be incremented and the msp430 should return to sleep. When this counter reach (45 * 60) seconds, this loop stops and the flow follow to make the antenna deployment.

Closed 2017-07-05.

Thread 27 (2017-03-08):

Read data from IMU

mfrata, 2017-03-08:
Read all the 14 bytes from the IMU
6 from Accelerometer
6 from gyroscope
2 from temperature

Closed 2017-04-04.

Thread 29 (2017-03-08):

Deploy antenna

eldertramontin, 2017-03-08:
Send a I2C command to arm and, in sequence, to open the antennas.
This should be tested in a similar module, since the antenna module can't be opened in tests.

Closed 2017-09-15.

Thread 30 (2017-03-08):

Test the IMU data

mfrata, 2017-03-08:
Check:
If when stands still the accel vector module is 1G or 9,79 m/s²
Test the three axis: X, Y, Z.
If when stands still the gyr values of yaw, pitch and roll are close to zero.

Closed 2019-04-11.

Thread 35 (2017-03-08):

Verify the msp430 temperature

eldertramontin, 2017-03-08:
Verify the correctness of the msp430 temperature.

eldertramontin, 2017-03-22:
Usando um multímetro, foi comparada a temperatura na superfície do MSP430 com o valor lido pelo sensor de temperatura interno. A diferença foi menor que 1ºC. Esta é provavelmente resultado do local onde a medição é feita com o multímetro (na superfície do MSP). Fisicamente não conseguimos medir no mesmo local. É necessário realizar um novo teste, em um dia com temperaturas mais baixas, para verificar se esta diferença mantém-se constante ou se altera-se em diferentes condições. As temperaturas deste teste ficaram em torno de 26ºC.

Closed 2017-05-12.

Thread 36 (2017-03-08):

Read the current sensing circuit

eldertramontin, 2017-03-08:
Change the code values of resistor and gain, and read the adc pin connected in the current sensing circuit.

eldertramontin, 2017-03-22:
Os valores de corrente calculados no firmware foram semelhantes aos reais. Foi utilizado um amperímetro para esta análise. Os valores lidos ficaram em torno de 10mA~11mA (o consumo pode mudar futuramente conforme forem adicionadas novas funcionalidades).

eldertramontin, 2017-04-06:
Foi realizada uma nova análise do sensor de corrente. Os dados podem ser observados na tabela abaixo:
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
O erro obtido é relativamente baixo, considerando a precisão dos componentes utilizados.

Closed 2017-03-22.

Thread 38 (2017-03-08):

SPI send

eldertramontin, 2017-03-08:
Create a SPI send function that send a byte.

mariobaldini, 2017-03-13:
Isso aqui não está implementado ainda?

mfrata, 2017-03-15:
Ele tem um library de SPI apenas com o cartão SD. Código que ele não vai mudar para nao quebrar o do cartão.

A proposta é fazer um drive mesmo, com no minimo as funções read, write e config.

Acho melhor deixar essa aqui pro arthur(carinha novo) que esta aprendendo spi no momento.

Closed 2017-05-03.

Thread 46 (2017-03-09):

Send Internal sensors data to the store data task

eldertramontin, 2017-03-09:
Send temperature, voltage and current through a queue.

mariobaldini, 2017-03-23:
Já existe uma task que lê periodicamente valores de sensores (ex: temperatura, corrente, etc..) e salva na memória nv?

eldertramontin, 2017-03-23:
Sim. Uma task lê os sensores e envia os dados a outra task que salva na memória não volátil.

mariobaldini, 2017-03-24:
Onde está documentado o formato de como esses dados são salvos na memória? (e como extrair/decodificar eles)

eldertramontin, 2017-03-27:
Não está. Vou verificar onde é melhor para documentar isso, criar uma issue referente e linkar assim que o fizer.

mariobaldini, 2017-03-29:
Blz.

Mas a documentação sempre tem q fazer parte da atividade em si. Organização e documentação do projeto tem mais importância do que código fonte em si (do primeiro é mais fácil chegar no segundo; do que o contrario).

Quando resolver uma issue, está implicito que o resultado foi propriamente documentado. Caso não tiver sido feito ainda, pode deixar pendente na propria issue (e não fechá-la ainda).

eldertramontin, 2017-04-04:
https://github.com/floripasat/obdh/blob/master/firmware/docs/packet_description.md#msp-sensors

Closed 2017-04-04.

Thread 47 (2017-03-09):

Read and calculate the supply voltage

eldertramontin, 2017-03-09:
Vref = 3V
Hardware v2.1 has a voltage divider (2:1) between 3V3 and GND to realize the measure.

Closed 2017-03-22.

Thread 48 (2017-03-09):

Read MSP430 internal temperature

eldertramontin, 2017-03-09:
Read the internal temperature sensor of MSP430F6659.

mfrata, 2017-03-15:
Eu coloquei ele na SPI. As memorias que trouxemos depois do cartão SD ainda não tem **nada** de código.

A principio estava falando com o Elder para deixar o SD para dados e a memoria para coisas auxiliares como log de telecommandos ou constantes para outros fins.

Portanto concordo com:

Documentar
Fazer testes
revisar o código e commitar no dev (elder revisa e depois passa pro master)

só que para o SPI e não para o ADC

Closed 2017-05-12.

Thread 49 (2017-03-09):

First boot information

eldertramontin, 2017-03-09:
Title;
Firmware version;
Hardware version;
Modules tests (clocks info, spi config info, i2c config info,etc) ;
"Boot completed"

mariobaldini, 2017-03-15:
Validar e fazer o merge no master

eldertramontin, 2017-03-15:
"Modules tests (clocks info, spi config info, i2c config info,etc) ;"
changed to:
"MSP peripheral tests (clocks) and setup info(clocks, uart, spi, i2c and adc) ;"

Modules tests will be splitted in new issues.

Closed 2017-03-15.

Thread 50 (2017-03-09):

Implementar a resposta a comandos de debug

eldertramontin, 2017-03-09:
Answer a command with a information:
COMMAND      |        RESPONSE
v                       |       OBDH voltage              
i                        |        OBDH current
t                        |       temperature
s                       |       systick

mariobaldini, 2017-03-13:
Os titulos das issues devem ser mais objetivos e associados com o bug/feat q será implementado em si (ie. primeira linha da commit msg).

Neste, por exemplo, nao dá pra entender se a issue é "requisitar a info de alguém",
ou implementar um comando q requisita alguma info

Reescreve o titulo e descrição pq nao consegui entender

Closed 2017-03-16.

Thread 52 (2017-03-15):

Minimal Assembly PCB 1

mfrata, 2017-03-15:
Soldering and tests of steps 1 to 16 described here: goo.gl/nFI1Of

mfrata, 2017-03-15:
O HW no git é o mais atualizado, ou seja, a versão 2.1.

Não posso dizer 100% funcional porque ainda não soldei tudo.

Closed 2017-03-15.

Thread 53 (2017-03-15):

Optimal Assembly PCB 1

mfrata, 2017-03-15:
Soldering an tests of steps 17 to 28 described here:  goo.gl/nFI1Of

mfrata, 2017-03-26:
Magnetorquer não foi testado. E segunda imu nao foi soldada

Closed 2017-03-26.

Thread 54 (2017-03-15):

Update git README.md with proper pointers to the official docummentation

mariobaldini, 2017-03-15:
Official OBDH docs (full detail) are stored in gdrive?

Insert a link into the readme, so a developer can easily go directly to the proper document and fix/review a documentation issue.

mfrata, 2017-03-16:
Ainda não movi para o drive.

Quero terminar de soldar pelo menos duas placas para o pessoal do SW ter hardware. Por enquanto vou colocar o link para o gitbooks

mariobaldini, 2017-03-16:
Nem coloca pro gitbooks. Ele já foi 'descontinuado' né?

Se sim, não vale gastar tempo com algo q vai ser morto. Já coloca direto por oficial.

mfrata, 2017-03-16:
Ja existe um ponteiro para la. Quando eu fizer mudança faço o commit e ja fecho essa issue

Closed 2019-04-11.

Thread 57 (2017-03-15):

Solar panel module test

eldertramontin, 2017-03-15:
Read some test registers to verify if the solar panel sensors are working.

mariobaldini, 2017-03-16:
Não tem como fazermos um "teste do painel solar". Pra começar q não temos nem interface direta com ele... só o EPS.

Acho que você quis dizer testar os sensores embarcados na placa do painel solar. (ie. iluminação, etc)
Mas isto é valido para o painel da gomspace... outra marca pode nem ter este sensor.

OBDH é um modulo por si só, genérico. Não pode ser projetado para uso restrito a um fabricante.

eldertramontin, 2017-03-16:
> "Acho que você quis dizer testar os sensores embarcados na placa do painel solar."

Isso. Realmente, eu quis dizer testar os sensores deles.

> "Pra começar q não temos nem interface direta com ele... só o EPS."

Temos interface direta com eles. USCI_B1, configurada como SPI, comunica com 3 paineis solares (um de cada eixo). Ela, atualmente, só serve para lermos a temperatura dos painéis. Além da SPI, também temos uma entrada para os _sun sensors_, como você falou, e uma saída para o _magnetorquer_ para cada um destes 3 paineis.

mariobaldini, 2017-03-16:
Não temos interface com eles. "Painel solar" é isto: https://solaerotech.com/wp-content/uploads/2015/03/Space-Solar-Cell.jpg
(na verdade é uma célula solar, sendo mais criterioso).
A saída é uma tensão. Só o EPS tem contato come eles. "Painel/celula solar" não tem SPI, etc..

Temos interface com um termometro, sun sensor, etc... que estão *localizados* no módulo do painel solar.

O "modulo do painel solar" é que seria a placa que contém as celulas, termometros, encaixes, etc... Os termos acabam ficando meio ambíguos mesmo (até a gomspace usa nomenclaturas meio estranhas).

É um detalhe meio bobo, mas conforme pudermos ser mais exatos nessas terminologias, economiza tempo no longo prazo (com erros... +5 minutos revisando oq é oq, etc).

PS: "detalhe bobo" não quer dizer q seja menos importante. Segue um clássico da eng de sw:
https://raygun.com/blog/2014/05/10-costly-software-errors-history/

NASA’s Mars Climate Orbiter (...) the engineering team failed to make a simple conversion from English units to metric.

mfrata, 2017-03-23:
https://rgsenergy.com/the-difference-between-solar-cells-and-solar-panels/

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

Closed 2019-04-11.

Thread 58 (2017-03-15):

Optimal Assembly PCB 2

mfrata, 2017-03-15:
Soldering an tests of steps 17 to 28 described here: goo.gl/nFI1Of

mfrata, 2017-03-29:
Devido a ISSUE PCB 2 - SPI1 Bus Bug #68 esta será fechada

Closed 2017-03-29.

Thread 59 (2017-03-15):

Minimal Assembly PCB 2

mfrata, 2017-03-15:
Soldering and tests of steps 1 to 16 described here: goo.gl/nFI1Of

mariobaldini, 2017-03-16:
Poderia revisar que placas estão sendo montadas?

As 3 q foram feitas em janeiro são a versão 2.0? (uma das que tenho aqui comigo).
e que tinham alguns bugs.

Os bugs foram corrigidos e agora em Março fabricadas as versões 2.1?

mfrata, 2017-03-16:
A versão 2.0 teve duas placas montadas. A que tu levou e a que o Elder ficou mexendo.

No momento estou montando as  da versão 2.1. Que tinha aqueles bugs "corrigidos".
Só vou ter certeza de que foram corrigidos depois que soldar tudo e fazer os testes minimos.

mfrata, 2017-03-29:
Devido a ISSUE PCB 2 - SPI1 Bus Bug #68 esta será fechada

Closed 2017-03-29.

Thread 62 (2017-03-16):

command line build documentation

mariobaldini, 2017-03-16:
Onde ficou documentado aquele processo de compilar e programar o msp430 via linha de comando, que vc desenvolveu no 'auto build system' ?

R-P-A, 2017-04-06:
Está em obdh/tools. Tem até um txt ali de documentação. Qualquer dúvida me avise.

Closed 2017-04-06.

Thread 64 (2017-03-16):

clock stabilization time is longer then expected

eldertramontin, 2017-03-16:
The wait time until the clock be stable is shorter then necessary. It is necessary add a longer delay (few seconds).

mariobaldini, 2017-03-16:
Poderia explicar um pouco mais?

Sobre o titulo, este ai está mais com cara de git commit, pois ele 'corrige' o erro. Para issues fica mais legível se for o erro em si (pode omitir que 'é necessário corrigir'). Isso vai estar implicito por uma label de 'bug', improvement, etc.

mariobaldini, 2017-03-16:
Mudei pra um exemplo ali do que acho q entendi.

Aquele 'too long' ali não está bom, pq é subjetivo e não especifico. O melhor seria ter algo mais objetivo, se viável

eldertramontin, 2017-03-17:
Modifiquei o título e a descrição. Espero que esteja mais claro. Basicamente é preciso só colocar um delay no codigo. Só criei a issue pra justificar a modificação.

Closed 2017-03-22.

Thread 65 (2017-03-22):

Verify the need of set the MSP Power Management Module

eldertramontin, 2017-03-22:
Para utilizar clocks elevados (acima de 8MHz) parece ser necessário configurar a tensão do core (Vcore). Verificar se há essa necessidade, visto que ainda não houve nenhum problema relacionado a isto.

mariobaldini, 2017-03-23:
@mfrata o clock do MSP já não estava maior que 8MHz?

Aquele vez q começamos a usar o cristal externo, não foi para poder deixar o MSP operando em clocks maiores que 8?

mfrata, 2017-03-23:
Isso é para clock interno redundante. Se o cristal falhar ficaremos com o clock padrão de 1,23 MHz. Portanto seria interessante configurar o clock interno para 16 MHz (assim como o externo), para caso ocorra falha apenas perderemos em precisão de velocidade nas execuções.

Apesar da importância, acho que isso tem que ser feito depois, de termos o minimo rodando

eldertramontin, 2017-03-23:
Na verdade essa issue é para verificar a necessidade de aumentar a tensão do core interno (Vcore). No datasheet diz que para clocks maiores que 8MHz isto faz-se necessário. Essa issue não chega a ser prioridade pois não temos nenhum problema em usar 16MHz, mesmo sem configurar o PMM conforme diz no datasheet. Então ela será tratada futuramente, se necessário for.

@mfrata, conforme seu comentário anterior, vou criar outra issue para tratar da configuração do oscilador interno (DCO), de maneira a ele ficar configurado a 16MHz também.

mariobaldini, 2017-03-24:
A idéia é o OBDH sempre rodar a 16 mhz;
a principio baseado no cristal externo;
que caso tiver algum problema vai fazer um fallback automatico pro interno
que também estará a 16 mhz (mas teria uma precisão um pouco menor)
?

eldertramontin, 2017-03-27:
Exatamente isso.

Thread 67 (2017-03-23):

Grants a clock redundancy

eldertramontin, 2017-03-23:
Makes the internal oscillator works on the same frequency of external clock source, so in a failure of the external crystal the uC clock will be approximately the same.

mariobaldini, 2017-03-24:
É possível detectar qual fonte de clock está sendo usada? (interno ou externo).

Se sim, coloca este parametro na lista dos 'dados internos' q são lidos e armazenados periodicamente.

eldertramontin, 2017-03-27:
É possível detectar se houve falha em alguma fonte de clock(cristal 1, cristal 2 e DCO), por meio de _fault flags_ (há uma para cada fonte de clock). Acho que poderia haver uma task para verificar estas e outras possíveis falhas. Acho que o termo é _housekeeping_ se não estou falando besteira.

mariobaldini, 2017-03-29:
Você respondeu que é possível detectar a falha;

Mas ainda estou em duvida sobre: É possível detectar qual fonte de clock está sendo usada?

(que seria independente de detecção de falha). Caso não existir falha alguma, é possível eu verificar e confirmar qual fonte está sendo usada *no momento*? (e não qual foi configurada no setup)

eldertramontin, 2017-03-29:
Uma correção referente a minha terminologia: estávamos usando "falhas" porém olhei novamente no datasheet e percebi que ele detecta "faltas". Ou seja, não necessariamente vão ocorrer falhas para que esta detecção ocorra.

Atualmente estamos configurados assim:
MCLK <= XT2 / 2
SMCLK <= XT2 / 2
ACLK <= XT1

Onde:
XT1 é o cristal 1, com frequência 32768Hz;
XT2 é o cristal 2, com frequência 32MHz;
MCLK é o clock principal, responsável pela frequência de execução das instruções. Nesta configuração = 16MHz.
SMCLK é o clock para subsistemas, que pode ser usado como frequência de referência para UART/I2C/SPI/ADC/Timers. Nesta configuração = 16MHz.
SMCLK é o clock para subsistemas, que pode ser usado como frequência de referência para UART/I2C/SPI/ADC/Timers. Nesta configuração = 32768Hz e é utilizado como base de tempo.

Em caso de falta no XT1, clocks associados a ele usarão o REFO como fonte de clock. Em caso de falta do XT2, clocks associados a ele usarão o DCO como fonte de clock. REFO opera a 32768Hz.
Atualmente o DCO ainda não está configurado para trabalhar a 16MHz, mas será feito. Então, mesmo em caso de uma falta detectada, não haveria mudança na frequência de trabalho, somente na precisão.

Agora respondendo a pergunta: É possível detectar qual fonte de clock está sendo usada?
Não exatamente. A partir do momento que for configurada uma fonte para determinado clock, se não houverem faltas, pode-se inferir que aquela fonte está sendo realmente usada. Se houver uma falta, a fonte de clock será alterada para DCO ou REFO, dependendo do cristal onde ela ocorreu. Então é possível estimar que determinada falta levou o sistema ao estado X ou Y, apenas lendo as _fault flags_.

Para retornar ao estado original, os _fault flags_ devem ser resetados. Se a falta persistir, eles serão automaticamente setados. Caso contrário, as configurações originais, anteriores a falta, serão restauradas.

eldertramontin, 2017-04-05:
Os clocks redundantes foram configurados. Para checar as fault flags foi aberta a issue #70.

Closed 2017-04-05.

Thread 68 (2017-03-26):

PCB 2 - SPI1 Bus Bug

mfrata, 2017-03-26:
O canal da spi1 da placa 2 está apresentando problemas.

Primeiramente havia um curto entre as linhas do barramento. Foi descoberto que este estava nos pinos do msp (A). Foi resoldado algumas vezes e por fim trocado por um msp(B).

O barramento não apresenta mais curto, porém a leitura com o cartão sd não funciona ainda.

Este barramento é critico pois alem do cartão sd, as memorias e os painéis estão conectados à ele.

Portanto preciso que seja verificado a integridade deste barramento na placa 2.

André e Arthur devem fazer testes usando uma launchpad para tentar se comunicar com o msp via spi. Devem observar as formas de onda no analizador lógico ou osciloscópio.

O André fará o código na launchpad e o Arthur(que ja esta fazendo um driver simples de spi) o ajudará no processo.

Se o problema for na pcb (trilhas do barramento) perderemos varias funções desta placa ou ela por inteiro.

PS: o msp(A) foi soldado na terceira placa junto com os circuitos do cartão sd, e não apresentaram problema nenhum. Portanto o problema não é interno ao chip ou ao cartão sd. E sim à placa 2.

mfrata, 2017-03-29:
Devido ao tempo que levara para encontrar o erro, e a incerteza de possibilidade de correção decidi deixar esta placa de lado.

Atualmente temos
1 placa v2.0 com:

1. msp
2. cristais
3. circuito de consumo de corrente total do obdh
4. circuito de referencia para o ADC
5. imu(9250)
6. sdcard
7. watchdog externo
8. 1 driver de corrente(magnetorquers)
9. 1 sensor de fotodiodo

1 versão 2.1 completa(exceto segunda imu(bosch))

1 versão 2.1 com o minimo soldado

mfrata, 2017-03-29:
Para essa PCB 3 - não soldaremos a segunda imu e nem os magnetorquers
Como essa placa será a da integração, não terá headers e nem devera ter algum fio soldado diretamente à pcb

mfrata, 2017-03-29:
Por fim ainda temos 1 placa da versão 2.0 que pode ser usada caso falte placas do obdh para os desenvolvedores do SW.

Totalizando 3 placas soldadas e um disponivel para solda.

mariobaldini, 2017-03-29:
Esse problema na SPI aconteceu na v2.1?

Foi um problema de fabricação/montagem ou pode ser de layout? Com certeza a parte de SPI no layout 2.0 e 2.1 é idêntica?

mfrata, 2017-03-30:
Especificamente na placa 2.

Muito provavel que tenha sido um problema de fabricação. Essas placas não tem qualidade muito boa. Vimos isso tanto no eps e ttc.

Sim o SPI das duas versões são identicas.

mariobaldini, 2017-03-30:
"Especificamente na placa 2."

2.0 ou 2.1?

Qual foi o fabricante?

mfrata, 2017-03-30:
2.1.

A versão 2.0 foi pela curta
A versão 2.1 foi pela Griffus

Closed 2017-04-04.

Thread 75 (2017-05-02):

Fix the I2C routine to agree with the requirements

eldertramontin, 2017-05-02:
Change the code to agree with the satellite definitions on
https://docs.google.com/document/d/1Ay4zeUjE7SGfaBFZPeS7ivnEsRm9Xsw-wQFbMZbaz18  (OBDH - EPS bus):

Closed 2017-05-02.

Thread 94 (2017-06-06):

Implements a event log in a non-volatile memory

eldertramontin, 2017-06-06:
Saves events such:
- reset cause
- telecommand arrival
- antenna deployment
- energy state change

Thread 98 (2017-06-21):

Implements a SPI interface through software

eldertramontin, 2017-06-21:
Creates a software that implements the SPI protocol over GPIOs without using a embedded peripheral SPI interface

mariobaldini, 2017-06-21:
Poderia descrever mais essa issue? E o motivo?

eldertramontin, 2017-06-21:
Precisamos de um canal de comunicação com a MCU do TT&C, porém não temos mais interfaces de comunicação livres (usamos 3 I²Cs, 2 SPIs e 1 UART). Já possuímos 4 GPIOs que ligam OBDH com TT&C, que já eram destinados para esta comunicação, porém sem um protocolo definido. Em vez de criar um protocolo novo, foi decidido utilizar o SPI, porém via software, para evitar mudanças no hardware entre modelo de engenharia v2 e modelo de vôo. Uma outra alternativa é utilizar o barramento I²C principal, onde já estão conectados EPS, OBDH e os 2 payloads. O receio é sobrecarregar o barramento, uma vez que outras equipes relataram problemas com I²C e colocar mais 1 nó no barramento aumenta as chances de ocorrer algum erro. Então, a opção atual é utilizar SPI, porém, se houver alguma dificuldade, podemos optar por utilizar o barramento I²C. Deu pra entender ou ficou confuso?

mariobaldini, 2017-06-21:
Onde está o diagrama de blocos dessa arquitetura nova? E da anterior também? Procurei eles aqui mas não achei.
Assim fica mais fácil pra entender o que foi necessário mudar (e implicou nesse novo requisito).

Closed 2017-07-05.

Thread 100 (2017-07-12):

Antenna simulation

andrempmattos, 2017-07-12:
Make a simulation that reproduces the functions of the ISIS Deployable Antenna System (AntS). The system shall be able to communicate over I²C protocol, read 4 switches and manage 4 actuators.

Closed 2017-09-15.

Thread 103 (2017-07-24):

Change the IMU read to twice the current frequency

eldertramontin, 2017-07-24:
Read Gyroscope and Accelerometer 2 times per second and store the readings of each second (will be stored 2 readings of each sensor at a time).

Closed 2017-09-15.

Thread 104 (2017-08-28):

Store the antennas deployment status on non-volatile memory

eldertramontin, 2017-08-28:
In case of communication failure, the OBDH must be able to know if the deployment was already done.

mariobaldini, 2017-08-31:
Quando gravar esta info, use bits redundantes.
Por ex:
Ao invés de usar 1 byte, com dois possíveis valores; use 3 e considere o valor da maioria. Assim se um for corrompido, vc ainda chega no status correto.

E cuidado quando fizer IFs/Switches de comparação para não esperar que as únicas opções sejam as previstas originalmente.
Ex:
0xAA - deployed
0xBB - não deployed

pode ocorrer um bitflip e vc ler depois 0xCC;
se isto não estiver previsto adequadamente na compração, não vai entrar em nenhum dos estados e talvez gerar algum bug.

Closed 2017-09-15.

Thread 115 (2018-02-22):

Fix a bug in the uSD card readings

eldertramontin, 2018-02-22:
The write/read in uSD it's not working properly. When some data frame was read it's values are all 0. Analyze and correct this mistake.

eldertramontin, 2018-04-13:
Done

Closed 2018-04-13.

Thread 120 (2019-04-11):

Change the downlink/uplink frequency to 436.1 MHz

mgm8, 2019-04-11:
Accordingly to the IARU frequencies coordination, the downlink and uplink frequencies must be 436.1 MHz.

Instructions about the radio module configuration can be found [here](https://github.com/floripasat/ttc/wiki/Radios-Configuration)

mgm8, 2019-04-22:
Downlink at 436.1 MHz (without frequency calibration):

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

mgm8, 2019-04-23:
Output frequency = 436.10025 MHz (no calibration required):

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

Output power = 26.61 dBm (radio input voltage = 3.3 V):

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

mgm8, 2019-04-25:
Uplink tested and working at 436.1 MHz

Closed 2019-04-25.

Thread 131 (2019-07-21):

Use of the equality operator to control a counter variable

mgm8, 2019-07-21:
**Problem**

When a counter variable is compared with another variable or value, in case of a bit flip event, using the equality operator can take a event to never happen or cause an unexpected behavior.

**Example**

https://github.com/floripasat/obdh/blob/3df34aba0a75eac281b79b53abce0e889b527bed/firmware/include/obdh.c#L172

> NOTE: Maybe there are more occurrences of this problem along the firmware, a further analysis must be performed.

**Solution**

Replace ```==``` by ```>=``` or a similar solution according to the respective routine.

Closed 2019-09-18.

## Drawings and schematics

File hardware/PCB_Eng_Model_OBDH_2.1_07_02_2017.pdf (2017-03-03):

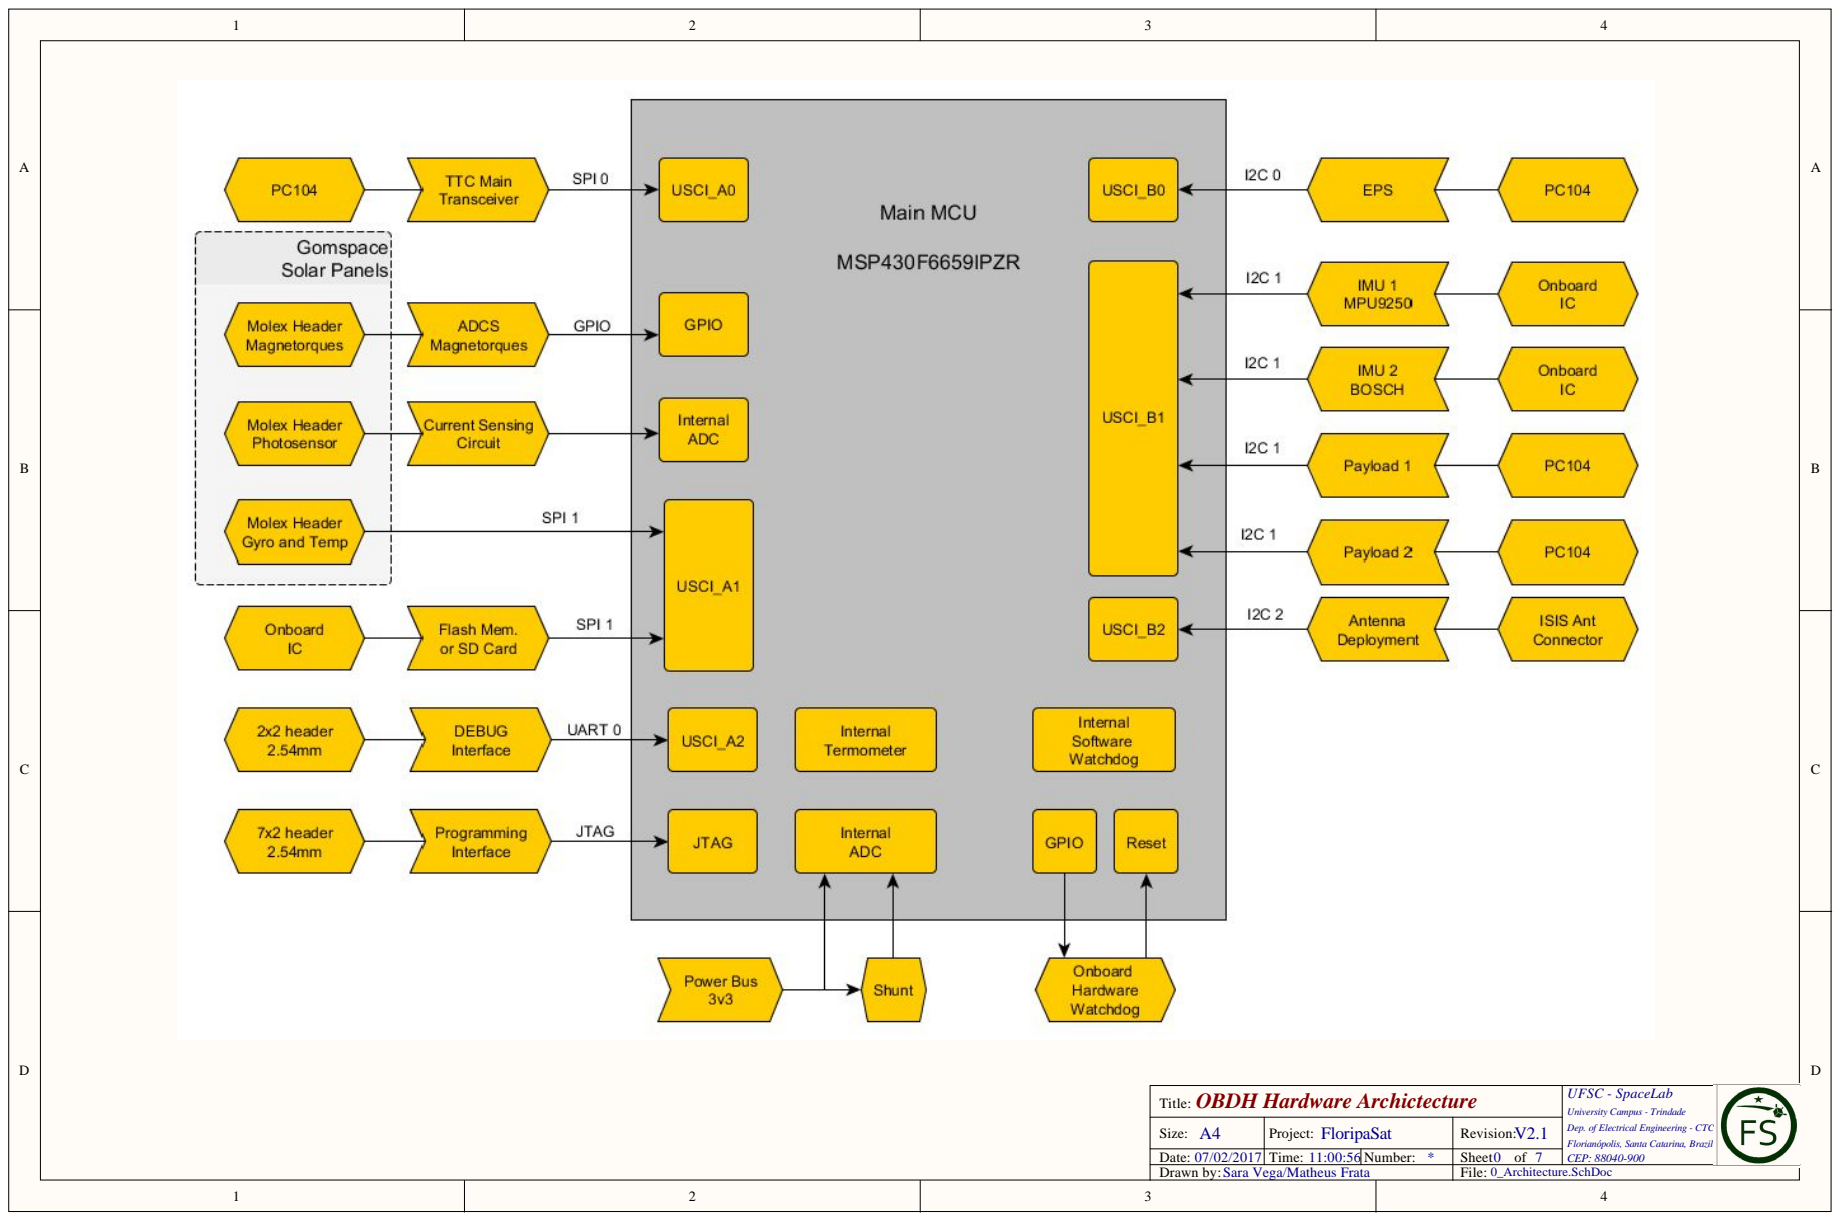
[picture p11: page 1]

OBDH Hardware Archictecture Title: | UFSC - SpaceLab University Campus - Trindade Dep. of Electrical Engineering - CTC Florianópolis, Santa Catarina, Brazil CEP: 88040-900

Size: A4 | Project: FloripaSat | Revision: V2.1

Date: 07/02/2017 | Time: 11:00:56 | Number: * | Sheet of 7
Drawn by:Sara Vega/Matheus Frata | File: 0_Architecture.SchDoc

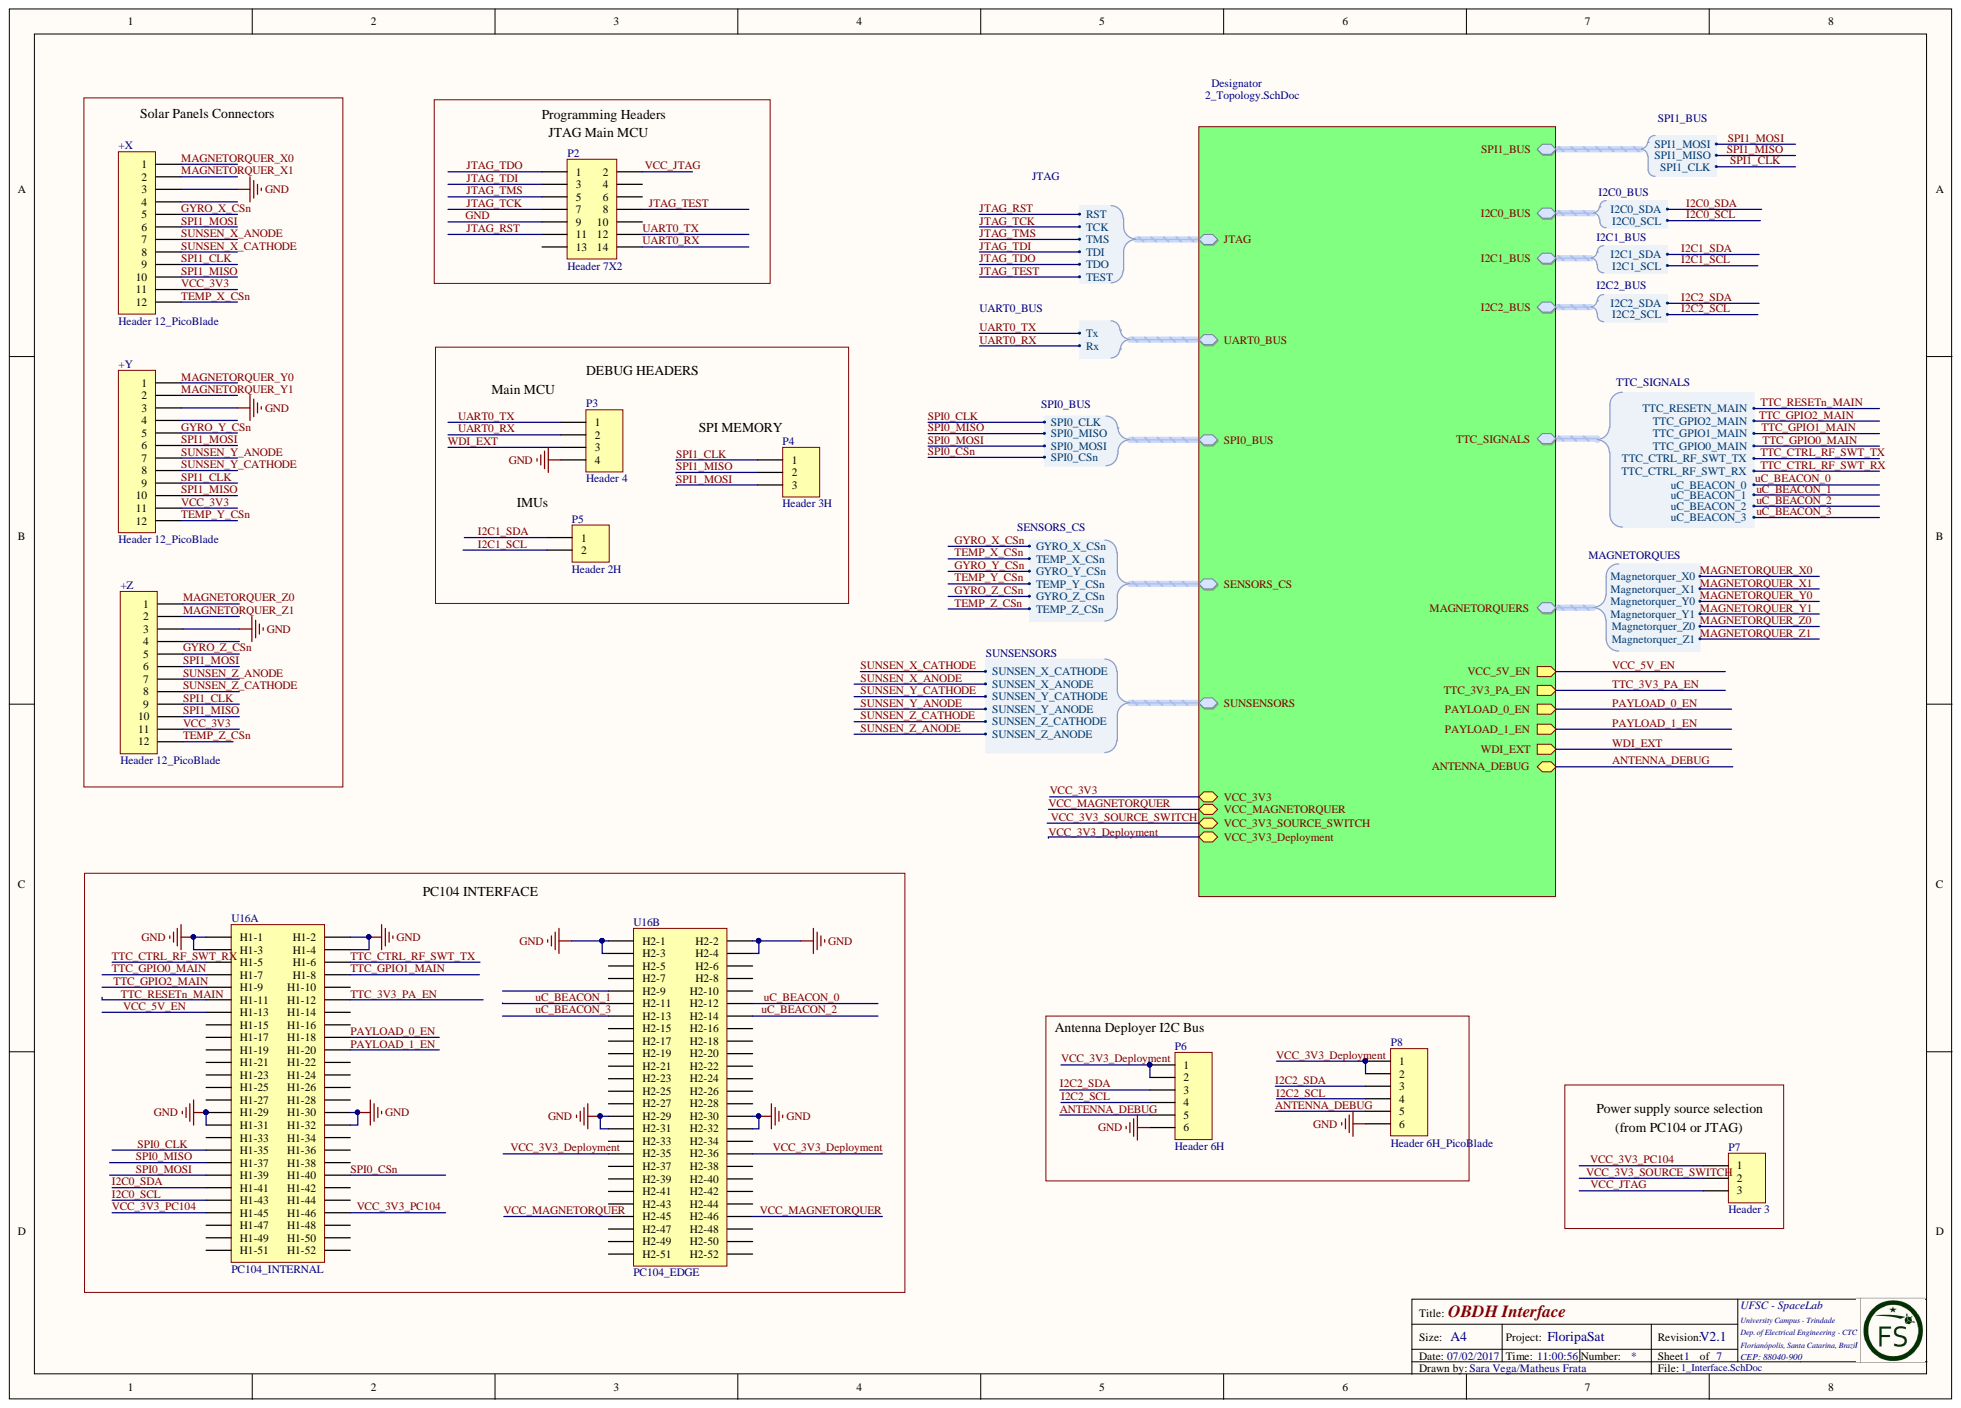
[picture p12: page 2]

OBD H In te rfac e T i t le: | UFSC - SpaceLab Univ e rsity Campus -Trindade Dep. of Ele ctrical Engine e ring -C T C Florian ópolis , Santa Catarina, B razil CEP : 88040-900

Size: A | Project : F loripa S a t | Revi s ion: V2.1

T i me: | Number : | Sheet of

D rawn by: Sara Vega/ Matheus Frat a | Fi le:

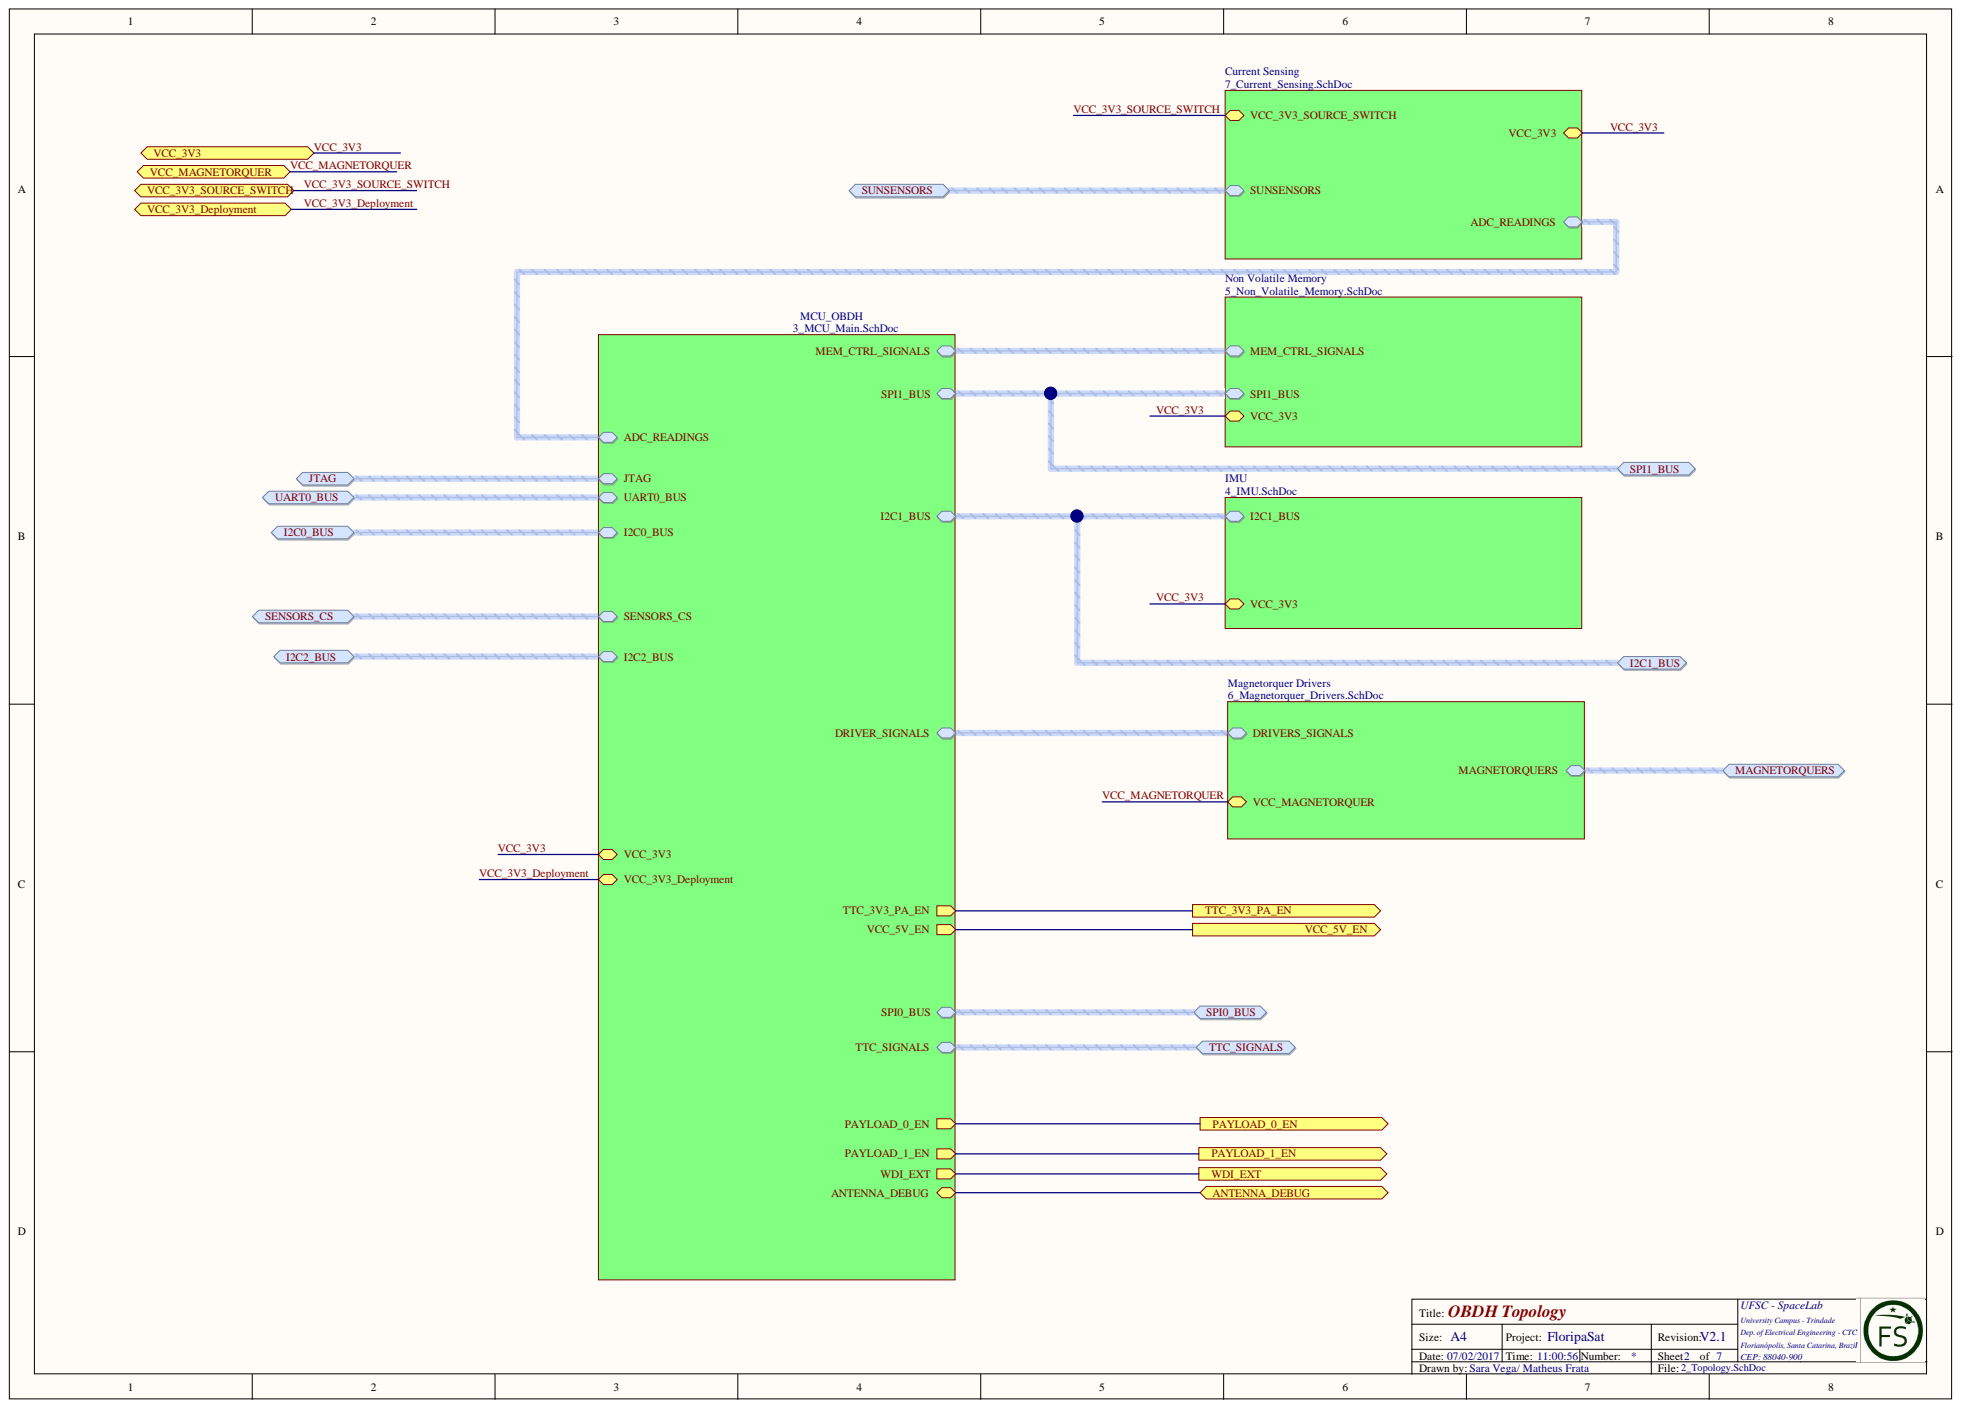
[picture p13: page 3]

OBDH Topology Title: | UFSC - SpaceLab University Campus - Trindade Dep. of Electrical Engineering - CTC Florianópolis, Santa Catarina, Brazil CEP: 88040-900

Size: A4 | Project: FloripaSat | Revision: V2.1

Drawn by: Sara Vega/ Matheus Frata

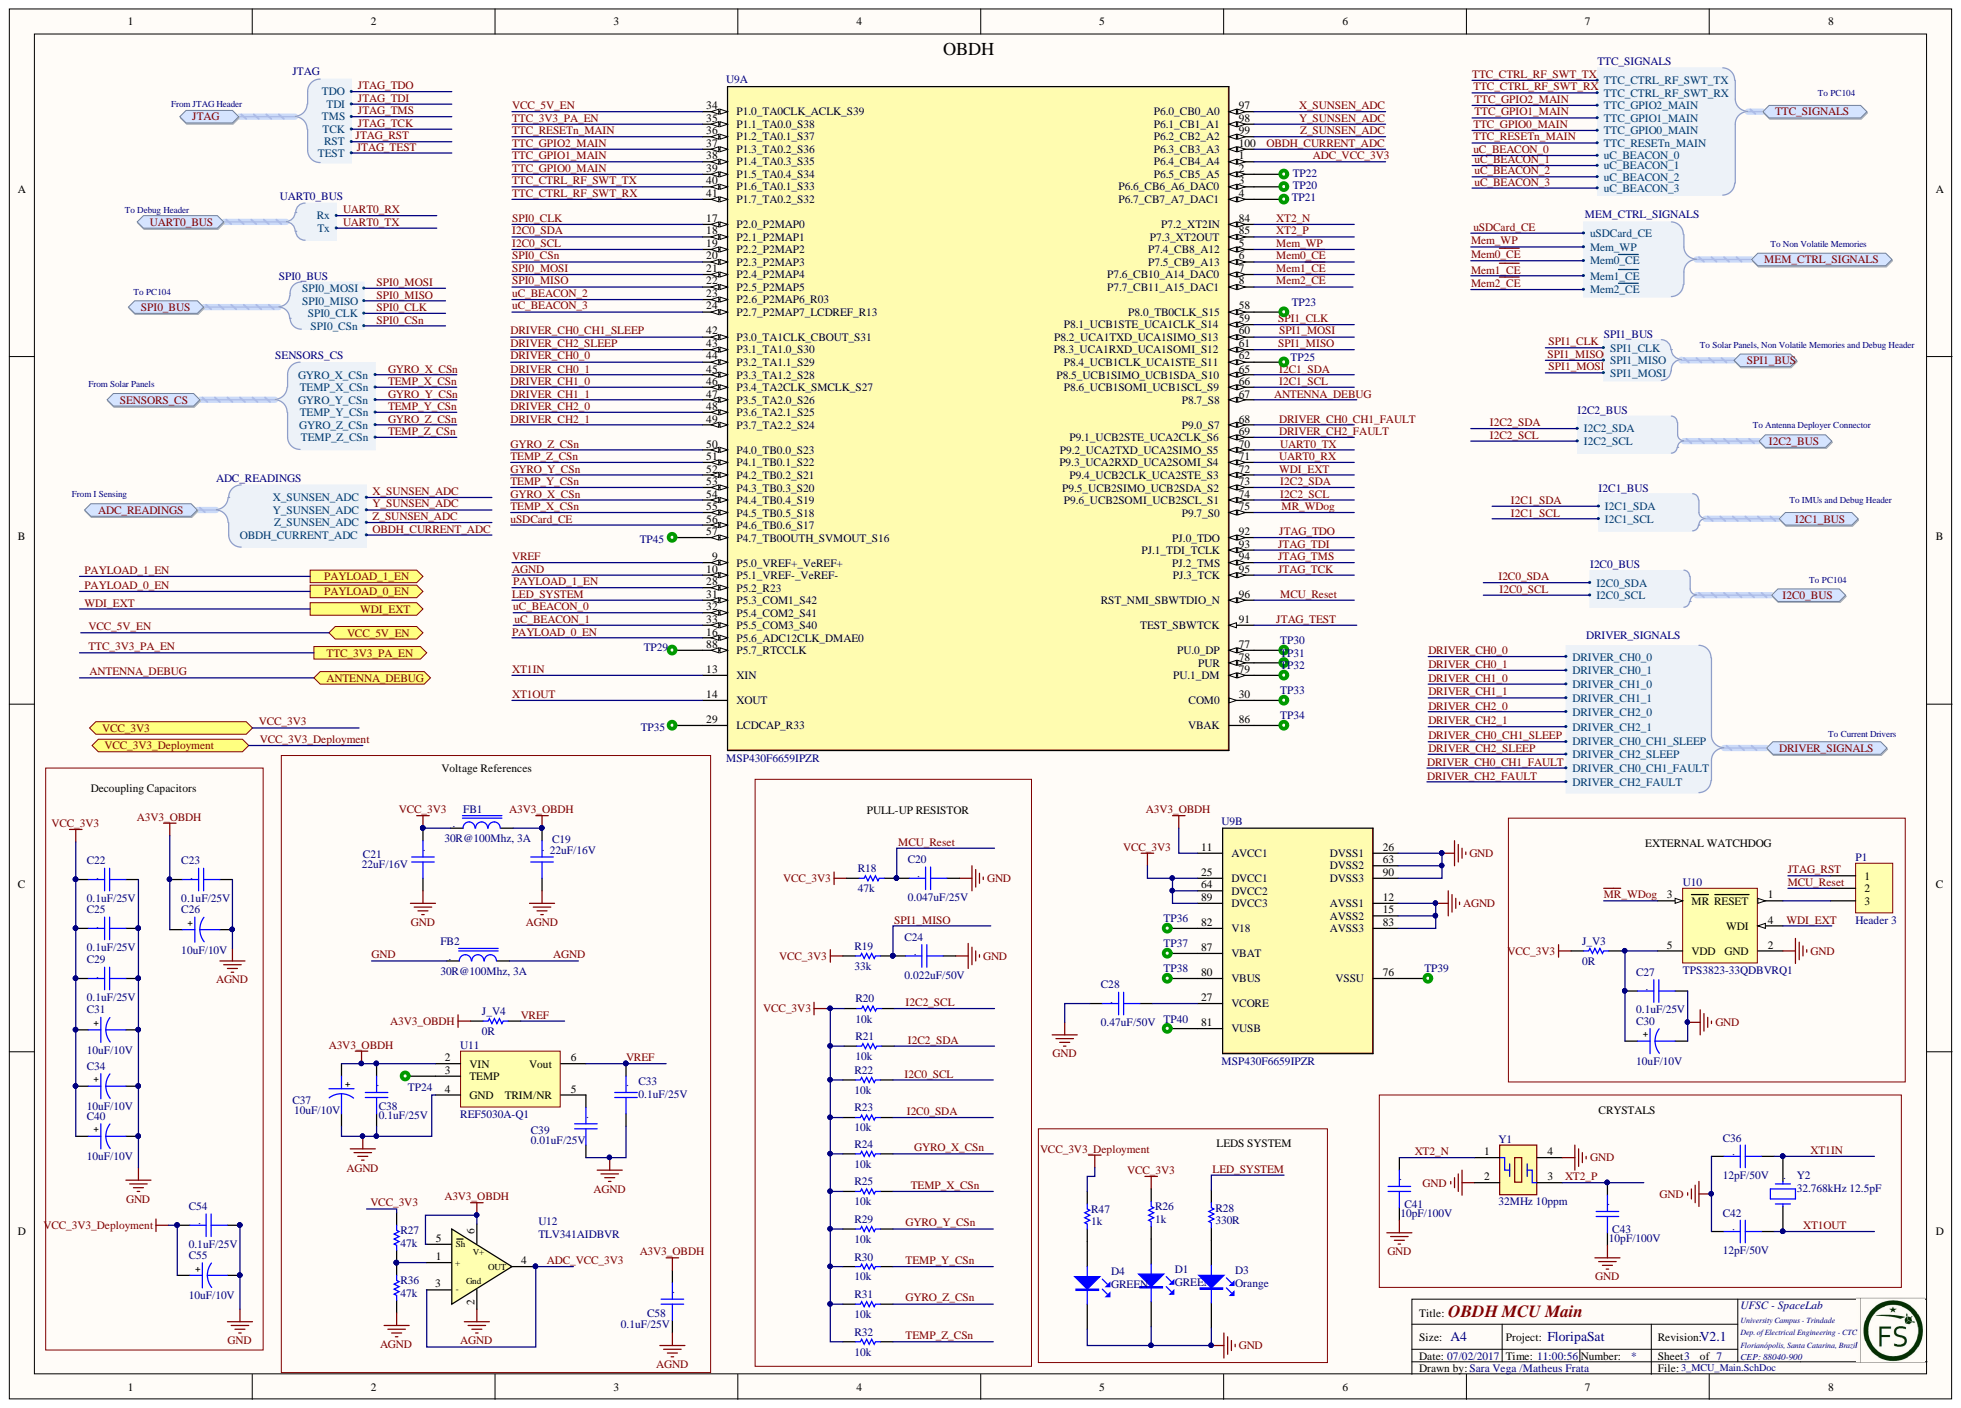
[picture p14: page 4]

To Non Volatile Memories
MEM_CTRL_SIGNALS

To Solar Panels, Non Volatile Memories and Debug Header

To Antenna Deployer Connector
I2C2_BUS

To IMUs and Debug Header
I2C1_BUS

VCC_3V3_Deployment R47 1k | R26 1k

OBDH MCU Main Title: | UFSC - SpaceLab University Campus - Trindade Dep. of Electrical Engineering - CTC Florianópolis, Santa Catarina, Brazil CEP: 88040-900

Drawn by: Sara Vega /Matheus Frata

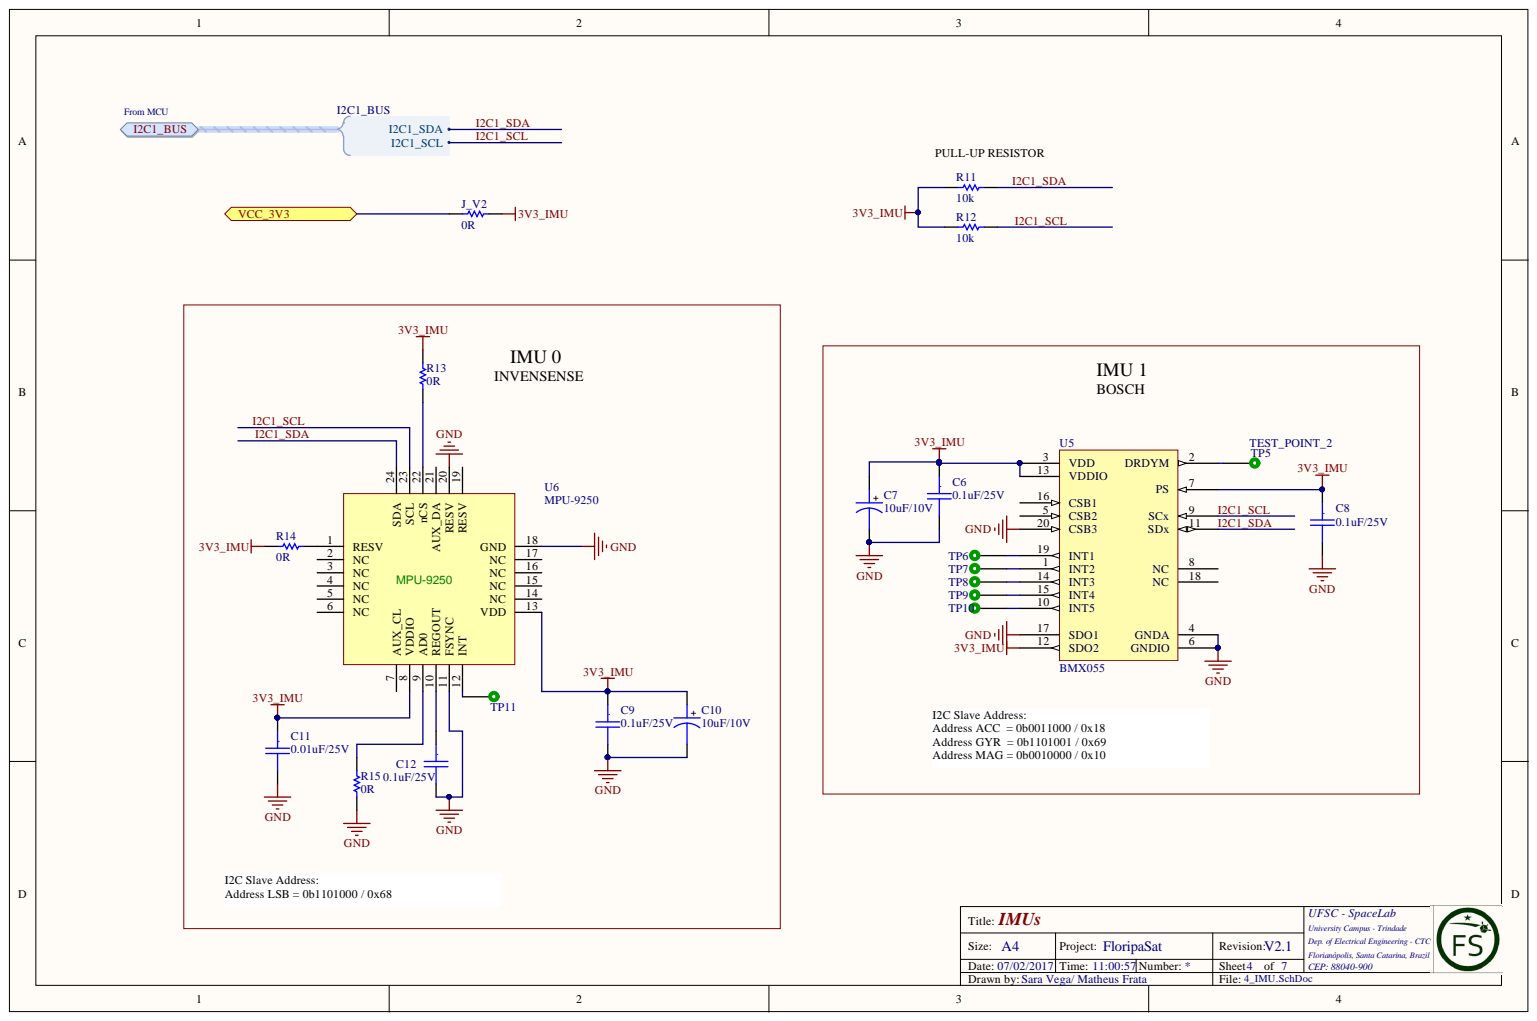
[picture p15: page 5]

IMUs Title: | UFSC - SpaceLab University Campus - Trindade Dep. of Electrical Engineering - CTC Florianópolis, Santa Catarina, Brazil CEP: 88040-900

Size: A4 | Project: FloripaSat | Revision: V2.1

Drawn by:Sara Vega/ Matheus Frata | 4_IMU.SchDoc

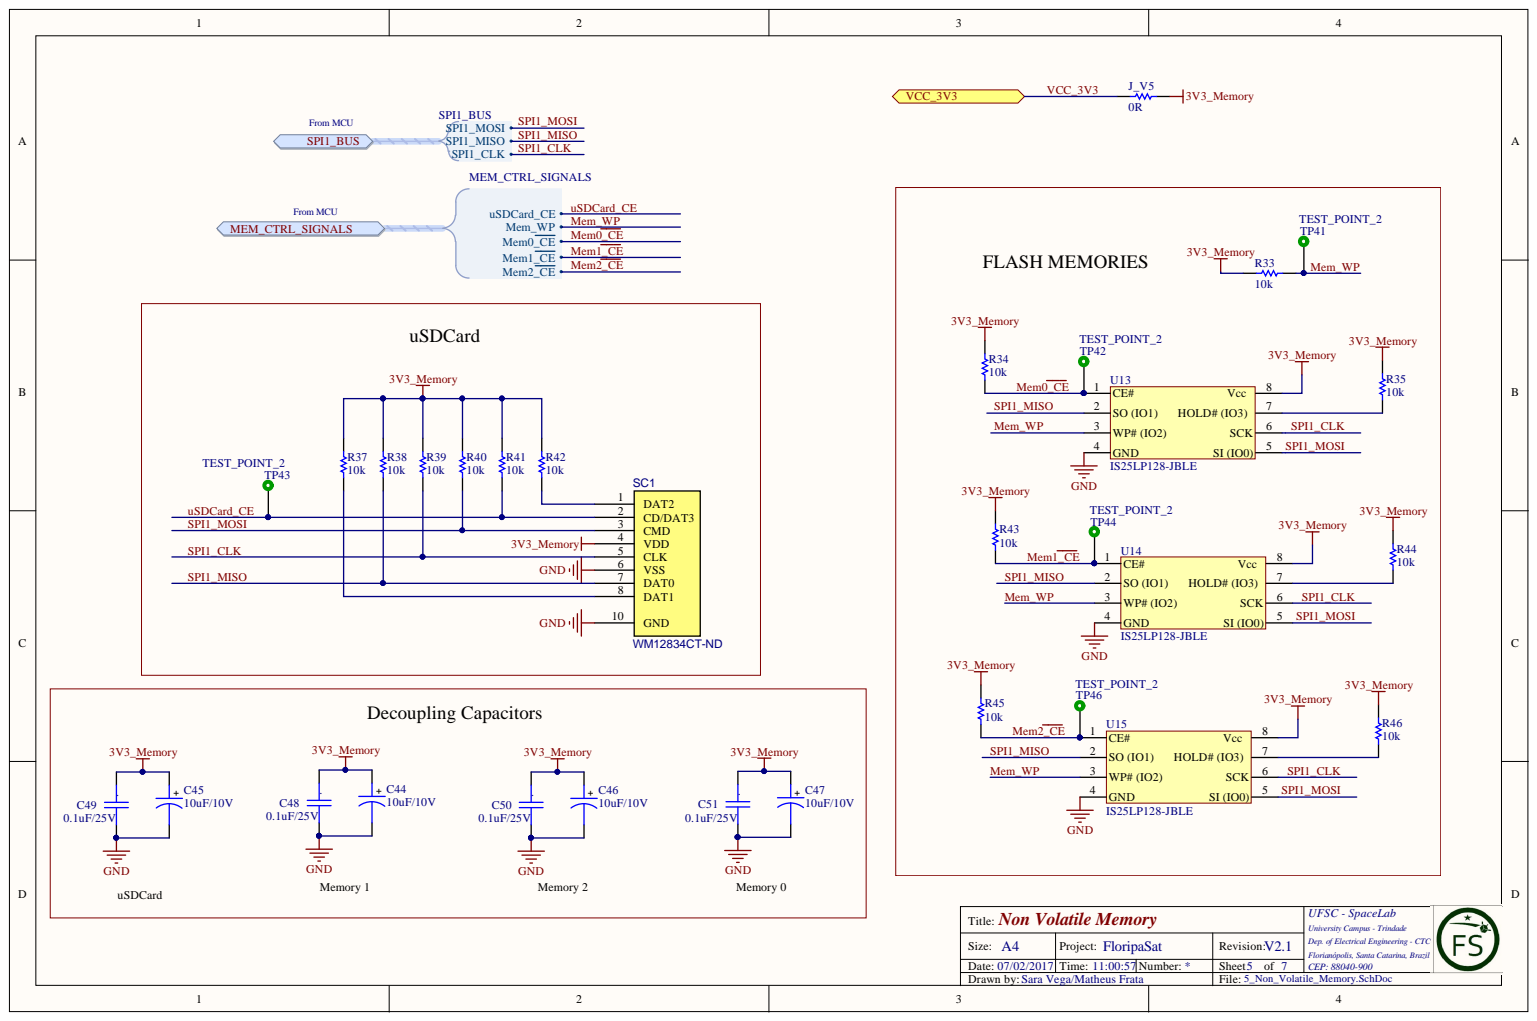
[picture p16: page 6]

Non Volatile Memory Title: | UFSC - SpaceLab University Campus - Trindade Dep. of Electrical Engineering - CTC Florianópolis, Santa Catarina, Brazil CEP: 88040-900

Size: A4 | Project: FloripaSat | Revision: V2.1

Drawn by:Sara Vega/Matheus Frata | 5_Non_Volatile_Memory.SchDoc

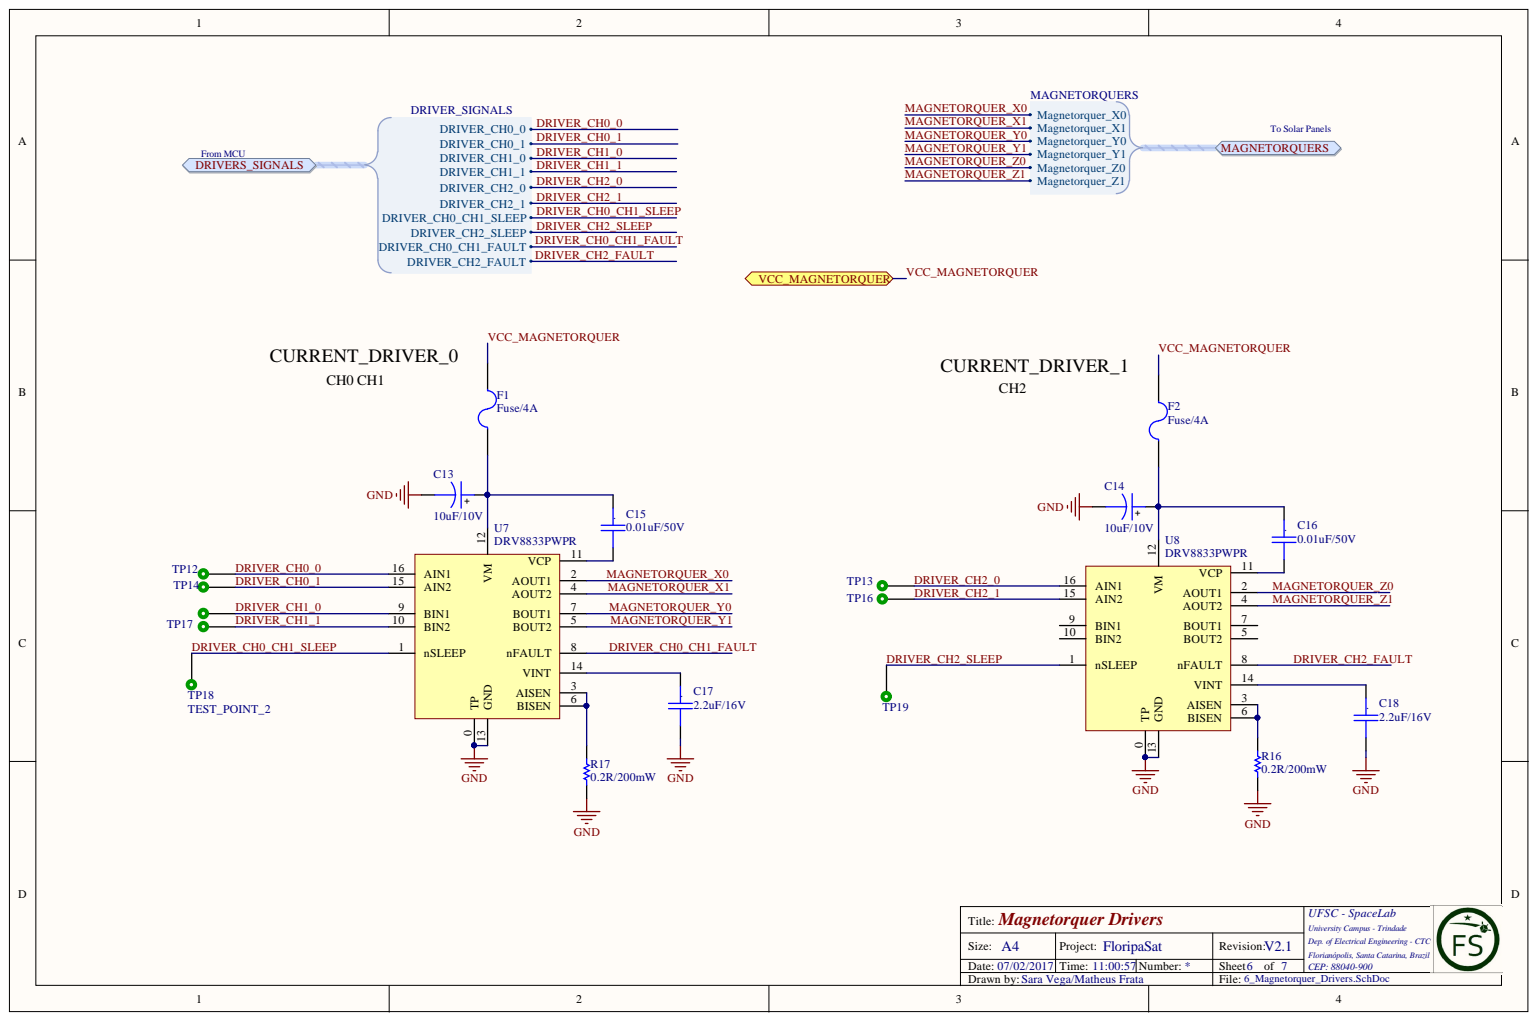
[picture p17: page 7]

Magnetorquer Drivers Title: | UFSC - SpaceLab University Campus - Trindade Dep. of Electrical Engineering - CTC Florianópolis, Santa Catarina, Brazil CEP: 88040-900

Size: A4 | Project: FloripaSat | Revision: V2.1

Drawn by:Sara Vega/Matheus Frata | 6_Magnetorquer_Drivers.SchDoc

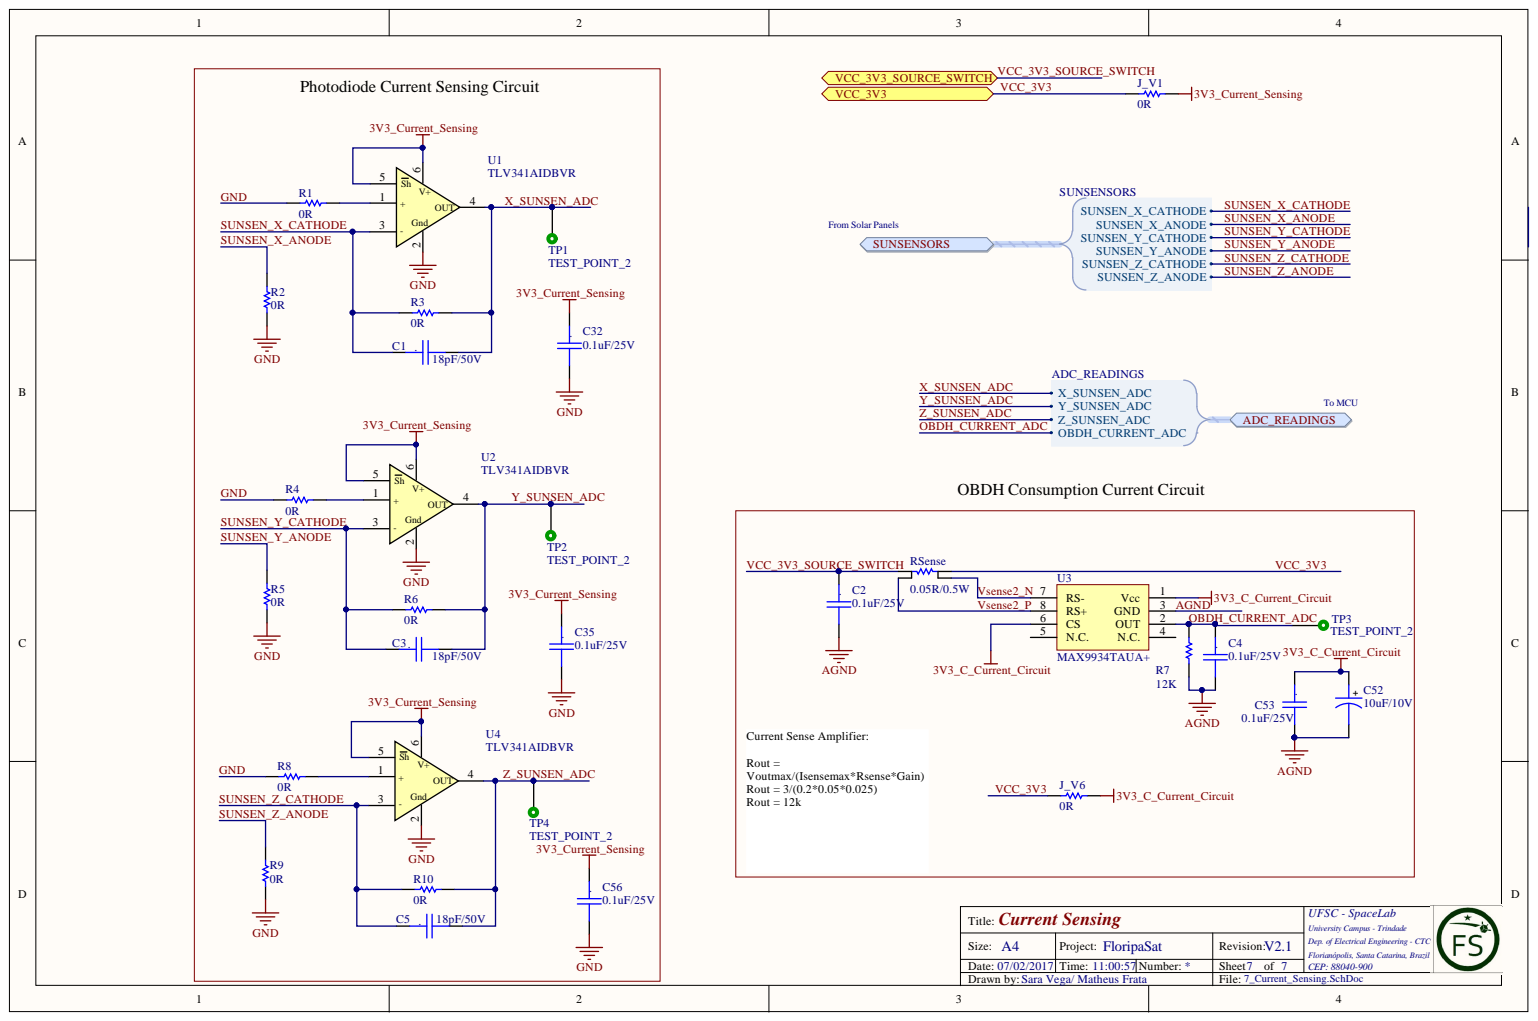
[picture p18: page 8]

Photodiode Current Sensing Circuit

OBDH Consumption Current Circuit

Current Sensing Title: | UFSC - SpaceLab University Campus - Trindade Dep. of Electrical Engineering - CTC Florianópolis, Santa Catarina, Brazil CEP: 88040-900

Size: A4 | Project: FloripaSat | Revision: V2.1

Drawn by:Sara Vega/ Matheus Frata | 7_Current_Sensing.SchDoc

Bill of Materials | Bill of Materials For Project [PCB_Eng_Model_OBDH_2.PrjPcb] (No PCB Document Selected)
Source Data From: | PCB_Eng_Model_OBDH_2.PrjPcb
Project: | | PCB_Eng_Model_OBDH_2.PrjPcb
Variant: | | None
Creation Date: 07/02/2017 | 11:01:11
Print Date: | 07-Feb-17 | 11:01:17 AM
#Column NameFootprin | Comment | PartNumber | Designator | Description | Quantity

HDR12 PicoBlade
- duplicate
| Header
| 12_PicoBlade | 53398-1271, 53398-1271,
| | 533981271 | +X, +Y, +Z | Header, 12-Pin | 3
CC0805 | 18pF/50V | CC0805JRNPO9BN180 | C1, C3, C5 | CAP CER 18pF 50V 5% X7R 0805 | 3
CC0805 | 0.1uF/25V | CC0805KRX7R8BB104 | C2, C4, C6, C8, C9, C12, C22, C23,
| | | C25, C27, C29, C32, C33, C35, C38,
| | | C48, C49, C50, C51, C53, C54, C56,
| | | C58 | CAP CER 0.1UF 25V 10% X7R 0805 | 23
CC0805_Tantalum | 10uF/10V | TPSP106M010R2000, TPSP106M010R2000, TPSP106M010R2000, TPSP106M010R2000, TPSR106K006R1000, TPSR106K006R1000, TPSR106K006R1000, TPSR106K006R1000, TPSR106K006R1000, TPSR106K006R1000, TPSP106M010R2000, TPSP106M010R2000, TPSP106M010R2000, TPSP106M010R2000, TPSP106M010R2000, TPSR106K006R1000

C7, C10, C13, C14, C26, C30, C31, C34, C37, C40, C44, C45, C46, C47, C52, C55

CAP Tantalum 10uF 10V 20% 0805, CAP Tantalum 10uF 10V 20% 0805, CAP Tantalum 10uF 10V 20% 0805, CAP Tantalum 10uF 10V 20% 0805, CAP Tantalum 10uF 6.3V 10% 0805, CAP Tantalum 10uF 6.3V 10% 0805, CAP Tantalum 10uF 6.3V 10% 0805, CAP Tantalum 10uF 6.3V 10% 0805, CAP Tantalum 10uF 6.3V 10% 0805, CAP Tantalum 10uF 6.3V 10% 0805, CAP Tantalum 10uF 10V 20% 0805, CAP Tantalum 10uF 10V 20% 0805, CAP Tantalum 10uF 10V 20% 0805, CAP Tantalum 10uF 10V 20% 0805, CAP Tantalum 10uF 10V 20% 0805, CAP Tantalum 10uF 6.3V 10% 0805

16
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

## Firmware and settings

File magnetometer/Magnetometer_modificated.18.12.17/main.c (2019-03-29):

#include <msp430.h>
#include "imu.h"
#include "math.h"
#include "flash.h"


/**
 * main.c
 */
int main(void)
{
    WDTCTL = WDTPW | WDTHOLD;  // stop watchdog timer
    int16_t mag_temp[3];
    uint8_t i = 0;
    float mag_max[3] = {-32767, -32767, -32767};
    float mag_min[3] = { 32767,  32767,  32767};

    float mag_x, mag_y, mag_z;
    float mag_x_calib_read, mag_y_calib_read, mag_z_calib_read;
    float sensors[7], sensors_buffer[7];


    float accel_x, accel_y, accel_z, temper;
    float accel_x_calib_read, accel_y_calib_read, accel_z_calib_read;

    float gyr_x, gyr_y, gyr_z;
    float gyr_x_calib_read, gyr_y_calib_read, gyr_z_calib_read;

    float X_ACC_CAL, Y_ACC_CAL, Z_ACC_CAL;


    uint8_t CALIBRATION_ACCELEROMETER;

    uint8_t n = 50.0;
    uint8_t YES = 1, NO = 0;
    float a= 256.096;
    float a1;

    i2c_setup(1);
    imu_setup();
    __delay_cycles(100000); //delay of 50 ms At 8 Hz ODR, new mag data is available every 125 ms

    mag_setup(1); //1 for Fuse ROM mode for Continuous measurement mode 1

        while(1)  //accelerometer and gyroscope
        {

           calibration_magnetometer(mag_max, mag_min, NO);
           calibration_accelerometer(NO);
           calibration_gyroscope(YES);


           mag_x_calib_read =  flash_read_float(CAL_X_MAG_ADDR_FLASH);
           mag_y_calib_read =  flash_read_float(CAL_Y_MAG_ADDR_FLASH);
           mag_z_calib_read =  flash_read_float(CAL_Z_MAG_ADDR_FLASH);

           accel_x_calib_read =  flash_read_float(CAL_X_ACCEL_ADDR_FLASH);
           accel_y_calib_read =  flash_read_float(CAL_Y_ACCEL_ADDR_FLASH);
           accel_z_calib_read =  flash_read_float(CAL_Z_ACCEL_ADDR_FLASH);
           gyr_x_calib_read =  flash_read_float(CAL_X_GYR_ADDR_FLASH);
           gyr_y_calib_read =  flash_read_float(CAL_X_GYR_ADDR_FLASH);
           gyr_z_calib_read =  flash_read_float(CAL_X_GYR_ADDR_FLASH);


         while(1)
         {
                 average(sensors_buffer, n);
                 read_magnetometer(mag_temp);

                 mag_x   = mag_temp[0] - mag_x_calib_read;
                 mag_y   = mag_temp[0] - mag_y_calib_read;
                 mag_z   = mag_temp[0] - mag_z_calib_read;

                 accel_x = (sensors_buffer[0] /n) - accel_x_calib_read; //average to 50 times and X current accelerometer
                 accel_y = (sensors_buffer[1] /n) - accel_y_calib_read; //average to 50 times
                 accel_z = (sensors_buffer[2] /n) - accel_z_calib_read;
                 temper  = (sensors_buffer[3] /n);  //average to 50 times
                 gyr_x   = (sensors_buffer[4] /n);   //average to 50 times
                 gyr_y   = (sensors_buffer[5] /n);  //average to 50 times
                 gyr_z   = (sensors_buffer[6] /n);   //average to 50 times

//               read_offset_accel(Off_accel);
    //             accel_x = sensors[0] - X_ACC_CAL;
               //  accel_y = sensors[1] - Y_ACC_CAL;
             //    accel_z = sensors[2] - Z_ACC_CAL;

                 __delay_cycles(50000); //F = 1Mhz
  }

        /*     while(1)  //magnetometer
        {
            sum_x = 0.0;
            sum_y = 0.0;
            sum_z = 0.0;
            for (j=0; j< measures_count; j++)  //get the the average of 50 measures
            {
                read_magnetometer(mag_temp);

              mag_temp2[0]= mag_temp[0] * (((ASA_X-128)*0.5/128.) + 1);
               mag_temp2[1]= mag_temp[1] * (((ASA_Y-128)*0.5/128.) + 1); //multiplication axe y by coefficient
               mag_temp2[2]= mag_temp[2] * (((ASA_Z-128)*0.5/128.) + 1); //multiplication axe z by coefficient


                mag_x_calibrated[j] = (mag_temp[0] - mag_offset[0]);  //calcule x calibrated
                sum_x = sum_x + mag_x_calibrated[j];                   // calculate of axe x

                mag_y_calibrated[j] = (mag_temp[1] - mag_offset[1]);  //calcule y calibrated
                sum_y = sum_y + mag_y_calibrated[j];                   // calculate sum of axe y

                mag_z_calibrated[j] = (mag_temp[2] - mag_offset[2]);  //calcule z calibrated
                sum_z = sum_z + mag_z_calibrated[j];                   //calculate sum of axe z
            }

            mag_x_average = sum_x/50.0;
            mag_x_calibrated_average = mag_x_average * (((ASA_X-128)*0.5/128.) + 1); //multiplication axis x by coefficient
            mag_y_average = sum_y/50.0;
            mag_y_calibrated_average= mag_y_average * (((ASA_Y-128)*0.5/128.) + 1); //multiplication axis y by coefficient
            mag_z_average = sum_z/50.0;
            mag_z_calibrated_average= mag_z_average * (((ASA_Z-128)*0.5/128.) + 1); //multiplication axis z by coefficient

            mag_root= sqrt(mag_x_average * mag_x_average + mag_y_average * mag_y_average + mag_z_average * mag_z_average);

         }

         */

        }
        return 0;
}
 

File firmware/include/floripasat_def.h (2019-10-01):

/*
 * floripasat_def.h
 *
 * Copyright (C) 2017-2019, Universidade Federal de Santa Catarina.
 *
 * This file is part of FloripaSat-OBDH.
 *
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
 */

 /**
 * \brief Project definitions, structures and macros
 *
 * \author Elder Tramontin
 * \author Gabriel Mariano Marcelino <gabriel.mm8@gmail.com>
 */

#ifndef FLORIPASATDEF_H_
#define FLORIPASATDEF_H_

#include <stdint.h>

#define SATELLITE_CALLSIGN                                  "PY0EFS"    /**< Satellite callsign. */

// Downlink packets
#define FLORIPASAT_PACKET_DOWNLINK_TELEMETRY                0x10        /**< Downlink packet with telemetry data. */
#define FLORIPASAT_PACKET_DOWNLINK_PING_ANSWER              0x11        /**< Ping answer. */
#define FLORIPASAT_PACKET_DOWNLINK_DATA_REQUEST_ANSWER      0x12        /**< Data request answer. */
#define FLORIPASAT_PACKET_DOWNLINK_HIBERNATION_FEEDBACK     0x13        /**< Hibernation feedback. */
#define FLORIPASAT_PACKET_DOWNLINK_CHARGE_RESET_FEEDBACK    0x14        /**< Charge reset feedback. */
#define FLORIPASAT_PACKET_DOWNLINK_MESSAGE_BROADCAST        0x15        /**< Message Broadcast. */
#define FLORIPASAT_PACKET_DOWNLINK_PAYLOAD_X_STATUS         0x16        /**< Payload X status. */
#define FLORIPASAT_PACKET_DOWNLINK_RUSH_FEEDBACK            0x17        /**< RUSH enable feedback. */
#define FLORIPASAT_PACKET_DOWNLINK_PAYLOAD_X_TELEMETRY      0x18        /**< Payload X telemetry. */

// Uplink packets
#define FLORIPASAT_PACKET_UPLINK_PING_REQUEST               0x20        /**< Ping request. */
#define FLORIPASAT_PACKET_UPLINK_DATA_REQUEST               0x21        /**< Data request. */
#define FLORIPASAT_PACKET_UPLINK_ENTER_HIBERNATION          0x22        /**< Enter hibernation. */
#define FLORIPASAT_PACKET_UPLINK_LEAVE_HIBERNATION          0x23        /**< Leave hibernation. */
#define FLORIPASAT_PACKET_UPLINK_CHARGE_RESET               0x24        /**< Charge reset. */
#define FLORIPASAT_PACKET_UPLINK_BROADCAST_MESSAGE          0x25        /**< Broadcast message. */
#define FLORIPASAT_PACKET_UPLINK_PAYLOAD_X_STATUS_REQUEST   0x26        /**< Payload X status request. */
#define FLORIPASAT_PACKET_UPLINK_PAYLOAD_X_SWAP             0x27        /**< Payload X swap. */
#define FLORIPASAT_PACKET_UPLINK_PAYLOAD_X_DATA_UPLOAD      0x28        /**< Payload data upload. */
#define FLORIPASAT_PACKET_UPLINK_RUSH_ENABLE                0x29        /**< RUSH enable. */
#define FLORIPASAT_PACKET_UPLINK_PAYLOAD_X_TELECOMMAND      0x2A        /**< Payload X telecommand. */

#define has_flag(x,y)   (x & y)

/**
 * \defgroup flags
 * \brief submodules flags of the data packet
 * \{
 */
#define  SYSTEM_STATUS_FLAG         BIT0
#define  IMU_FLAG                   BIT1
#define  OBDH_MISC_FLAG             BIT2
#define  SOLAR_PANELS_SENSORS_FLAG  BIT3
#define  MAIN_RADIO_FLAG            BIT4

#define  SOLAR_PANELS_FLAG          BIT5
#define  EPS_MISC_FLAG              BIT6
#define  BATTERY_MONITOR_FLAG       BIT7
#define  TEMPERATURES_FLAG          BIT8
#define  TASK_SCHEDULER_FLAG        BIT9

#define  PAYLOAD_RUSH_FLAG          BITA
#define  PAYLOAD_BRAVE_FLAG         BITB

/*
    *  This flag aware the GS to ignore the other flags, since the content
    *  of the frame is the whole data, and may disagree with the indication
    *  provided by the bit-flags.
    */
#define  WHOLE_ORBIT_DATA_FLAG      BITF

#define  ALL_FLAGS                  0xFFFF

//! \} End of flags

/**
 * \struct request_packet_t
 *
 * \brief The struct to decode a request command
 */
typedef struct {
    uint16_t flags;         /**< modules flags to request just the wanted data*/
    uint8_t packages_count; /**< number of packages to read, from offset */
    uint8_t packages_origin;/**< position used as reference for the offset */
    int32_t packages_offset;/**< number of packages to offset from origin */
} request_data_packet_t;

#define ARGUMENT_LENGTH 84

typedef struct {
    uint8_t id;                 /**< Packet ID code. */
    uint8_t src_callsign[7];    /**< Source callsign. */
    uint8_t data[220];          /**< Packet data. */
    uint16_t data_len;          /**< Packet data length in bytes. */
} telecommand_t;

#define PACKET_LENGTH   122  /**< according NGHAM packet sizes */

typedef struct {
    uint8_t type;
    union{
        struct{
            uint8_t segment[192];
            uint8_t segment_number;
        }ccsds_telemetry;
        struct {
            uint8_t status_segment[200];
            uint16_t segment_number;
        }bitstream_status_replay;
    }data;
} payload_brave_downlink_t;

typedef struct {
    uint8_t type;
    union{
        uint8_t bitstream_upload[84];
        uint8_t ccsds_telecommand[82];
        uint8_t status_argument[2];
    }data;
} payload_brave_uplink_t;
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

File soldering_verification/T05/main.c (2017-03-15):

//*******************************************************************************
//  MSP-MMC Demo - Demo to show how to use the MMC library
//
//  Description; This example shows the correct setup and usage of the MMC
//  Library
//
//
//  S. Schauer
//  Texas Instruments, Inc
//  March 2008
//  V1.1: Updated for IAR Embedded Workbench Version: 5.10
//  V1.2: fixed fill of buffer (buffer size overrun)
//******************************************************************************

/*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
* IN NO EVENT SHALL TI BE LIABLE FOR ANY SPECIAL, INCIDENTAL,
* CONSEQUENTIAL OR INDIRECT DAMAGES, HOWEVER CAUSED, ON ANY
* THEORY OF LIABILITY AND WHETHER OR NOT TI HAS BEEN ADVISED
* OF THE POSSIBILITY OF SUCH DAMAGES, ARISING IN ANY WAY OUT
* OF THIS AGREEMENT, THE PROGRAM, OR YOUR USE OF THE PROGRAM.
* EXCLUDED DAMAGES INCLUDE, BUT ARE NOT LIMITED TO, COST OF
* REMOVAL OR REINSTALLATION, COMPUTER TIME, LABOR COSTS, LOSS
* OF GOODWILL, LOSS OF PROFITS, LOSS OF SAVINGS, OR LOSS OF
* USE OR INTERRUPTION OF BUSINESS. IN NO EVENT WILL TI'S
* AGGREGATE LIABILITY UNDER THIS AGREEMENT OR ARISING OUT OF
* YOUR USE OF THE PROGRAM EXCEED FIVE HUNDRED DOLLARS
* (U.S.$500).
*
* Unless otherwise stated, the Program written and copyrighted
* by Texas Instruments is distributed as "freeware".  You may,
* only under TI's copyright in the Program, use and modify the
* Program without any charge or restriction.  You may
* distribute to third parties, provided that you transfer a
* copy of this license to the third party and the third party
* agrees to these terms by its first use of the Program. You
* must reproduce the copyright notice and any other legend of
* ownership on each copy or partial copy, of the Program.
*
* You acknowledge and agree that the Program contains
* copyrighted material, trade secrets and other TI proprietary
* information and is protected by copyright laws,
* international copyright treaties, and trade secret laws, as
* well as other intellectual property laws.  To protect TI's
* rights in the Program, you agree not to decompile, reverse
* engineer, disassemble or otherwise translate any object code
* versions of the Program to a human-readable form.  You agree
* that in no event will you alter, remove or destroy any
* copyright notice included in the Program.  TI reserves all
* rights not specifically granted under this license. Except
* as specifically provided herein, nothing in this agreement
* shall be construed as conferring by implication, estoppel,
* or otherwise, upon you, any license or other right under any
* TI patents, copyrights or trade secrets.
*
* You may not use the Program in non-TI devices.
* ********************************************************* */



#include <msp430.h>
#include "hal_hardware_board.h"
#include "mmc.h"
#include <stdio.h>

unsigned long cardSize = 0;
unsigned char status = 1;
unsigned int timeout = 0;

int i = 0;

unsigned char buffer[512];
int cont;
int main( void )
{
  WDTCTL = WDTPW + WDTHOLD;
  P5DIR |= BIT3;
  P5OUT &= ~BIT3;
  //Initialisation of the MMC/SD-card
  while (status != 0)                       // if return in not NULL an error did occur and the
                                            // MMC/SD-card will be initialized again
  {
    status = mmcInit();
    timeout++;
    if (timeout == 150)                      // Try 50 times till error
    {
      //printf ("No MMC/SD-card found!! %x\n", status);
      break;
    }
  }

  while ((mmcPing() != MMC_SUCCESS));      // Wait till card is inserted

  // Read the Card Size from the CSD Register
  cardSize =  mmcReadCardSize();

  if(cardSize > 0)
      P5OUT |= BIT3;
  else
      while(1);
//  Clear Sectors on MMC
//  for (i = 0; i < 512; i++) buffer[i] = 0;
//  mmcWriteSector(0, buffer);                // write a 512 Byte big block beginning at the (aligned) adress
//
  unsigned char outBuffer[256];
  mmcReadSector(1, outBuffer);
  char c;
  sscanf(outBuffer, "%c", &c);
  if(c != '#') {
      cont = 0;
  }
  else {
      sscanf(outBuffer, "%d", &cont);
      cont++;
  }
  sprintf(buffer,"#%d (autogenerated counter) - SD card test.\n", cont);

//  for (i = 0; i < 256; i++) buffer[i] = i;
  mmcWriteSector(1, buffer);                // write a 512 Byte big block beginning at the (aligned) adress

  int i;
  for(i = 0; i < cont; i++)
  {
      __delay_cycles(500000);
      P5OUT ^= BIT3;
      __delay_cycles(500000);
      P5OUT ^= BIT3;
  }

//  unsigned char outBuffer[256];
//  mmcReadSector(1, outBuffer);                 // read a size Byte big block beginning at the address.
//  for (i = 0; i < 512; i++) if(buffer[i] != 0) P1OUT |= 0x01;
  while(10);


  /***************************** STOOOOOOOOOOOOOOOOOOOOOOOOP    **********************************/


//  mmcReadSector(1, buffer);                 // read a size Byte big block beginning at the address.
//  for (i = 0; i < 512; i++) if(buffer[i] != 0) P1OUT |= 0x02;


// Write Data to MMC
//  for (i = 0; i < 512; i++) buffer[i] = i;
//  mmcWriteSector(0, buffer);                // write a 512 Byte big block beginning at the (aligned) adress
//
//  for (i = 0; i < 512; i++) buffer[i] = i+64;
//  mmcWriteSector(1, buffer);                // write a 512 Byte big block beginning at the (aligned) adress

  mmcReadSector(0, buffer);                 // read a size Byte big block beginning at the address.
  for (i = 0; i < 512; i++) if(buffer[i] != (unsigned char)i) P1OUT |= 0x04;

  mmcReadSector(1, buffer);                 // read a size Byte big block beginning at the address.
  for (i = 0; i < 512; i++) if(buffer[i] != (unsigned char)(i+64)) P1OUT |= 0x08;

  for (i = 0; i < 512; i++)
    mmcReadSector(i, buffer);               // read a size Byte big block beginning at the address.

  mmcGoIdle();                              // set MMC in Idle mode

  while (1);
}

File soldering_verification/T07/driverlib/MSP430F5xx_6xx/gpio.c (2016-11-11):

/* --COPYRIGHT--,BSD
 * Copyright (c) 2016, Texas Instruments Incorporated
 * All rights reserved.
 *
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
 * *  Redistributions of source code must retain the above copyright
 *    notice, this list of conditions and the following disclaimer.
 *
 * *  Redistributions in binary form must reproduce the above copyright
 *    notice, this list of conditions and the following disclaimer in the
 *    documentation and/or other materials provided with the distribution.
 *
 * *  Neither the name of Texas Instruments Incorporated nor the names of
 *    its contributors may be used to endorse or promote products derived
 *    from this software without specific prior written permission.
 *
 * THIS SOFTWARE IS PROVIDED BY THE COPYRIGHT HOLDERS AND CONTRIBUTORS "AS IS"
 * AND ANY EXPRESS OR IMPLIED WARRANTIES, INCLUDING, BUT NOT LIMITED TO,
 * THE IMPLIED WARRANTIES OF MERCHANTABILITY AND FITNESS FOR A PARTICULAR
 * PURPOSE ARE DISCLAIMED. IN NO EVENT SHALL THE COPYRIGHT OWNER OR
 * CONTRIBUTORS BE LIABLE FOR ANY DIRECT, INDIRECT, INCIDENTAL, SPECIAL,
 * EXEMPLARY, OR CONSEQUENTIAL DAMAGES (INCLUDING, BUT NOT LIMITED TO,
 * PROCUREMENT OF SUBSTITUTE GOODS OR SERVICES; LOSS OF USE, DATA, OR PROFITS;
 * OR BUSINESS INTERRUPTION) HOWEVER CAUSED AND ON ANY THEORY OF LIABILITY,
 * WHETHER IN CONTRACT, STRICT LIABILITY, OR TORT (INCLUDING NEGLIGENCE OR
 * OTHERWISE) ARISING IN ANY WAY OUT OF THE USE OF THIS SOFTWARE,
 * EVEN IF ADVISED OF THE POSSIBILITY OF SUCH DAMAGE.
 * --/COPYRIGHT--*/
//*****************************************************************************
//
// gpio.c - Driver for the gpio Module.
//
//*****************************************************************************

//*****************************************************************************
//
//! \addtogroup gpio_api gpio
//! @{
//
//*****************************************************************************

#include "inc/hw_memmap.h"

#ifdef __MSP430_HAS_PORT1_R__
#include "gpio.h"

#include <assert.h>

static const uint16_t GPIO_PORT_TO_BASE[] = {
    0x00,
#if defined(__MSP430_HAS_PORT1_R__)
    __MSP430_BASEADDRESS_PORT1_R__,
#elif defined(__MSP430_HAS_PORT1__)
    __MSP430_BASEADDRESS_PORT1__,
#else
    0xFFFF,
#endif
#if defined(__MSP430_HAS_PORT2_R__)
    __MSP430_BASEADDRESS_PORT2_R__,
#elif defined(__MSP430_HAS_PORT2__)
    __MSP430_BASEADDRESS_PORT2__,
#else
    0xFFFF,
#endif
#if defined(__MSP430_HAS_PORT3_R__)
    __MSP430_BASEADDRESS_PORT3_R__,
#elif defined(__MSP430_HAS_PORT3__)
    __MSP430_BASEADDRESS_PORT3__,
#else
    0xFFFF,
#endif
#if defined(__MSP430_HAS_PORT4_R__)
    __MSP430_BASEADDRESS_PORT4_R__,
#elif defined(__MSP430_HAS_PORT4__)
    __MSP430_BASEADDRESS_PORT4__,
#else
    0xFFFF,
#endif
#if defined(__MSP430_HAS_PORT5_R__)
    __MSP430_BASEADDRESS_PORT5_R__,
#elif defined(__MSP430_HAS_PORT5__)
    __MSP430_BASEADDRESS_PORT5__,
#else
    0xFFFF,
#endif
#if defined(__MSP430_HAS_PORT6_R__)
    __MSP430_BASEADDRESS_PORT6_R__,
#elif defined(__MSP430_HAS_PORT6__)
    __MSP430_BASEADDRESS_PORT6__,
#else
    0xFFFF,
#endif
#if defined(__MSP430_HAS_PORT7_R__)
    __MSP430_BASEADDRESS_PORT7_R__,
#elif defined(__MSP430_HAS_PORT7__)
    __MSP430_BASEADDRESS_PORT7__,
#else
    0xFFFF,
#endif
#if defined(__MSP430_HAS_PORT8_R__)
    __MSP430_BASEADDRESS_PORT8_R__,
#elif defined(__MSP430_HAS_PORT8__)
    __MSP430_BASEADDRESS_PORT8__,
#else
    0xFFFF,
#endif
#if defined(__MSP430_HAS_PORT9_R__)
    __MSP430_BASEADDRESS_PORT9_R__,
#elif defined(__MSP430_HAS_PORT9__)
    __MSP430_BASEADDRESS_PORT9__,
#else
    0xFFFF,
#endif
#if defined(__MSP430_HAS_PORT10_R__)
    __MSP430_BASEADDRESS_PORT10_R__,
#elif defined(__MSP430_HAS_PORT10__)
    __MSP430_BASEADDRESS_PORT10__,
#else
    0xFFFF,
#endif
#if defined(__MSP430_HAS_PORT11_R__)
    __MSP430_BASEADDRESS_PORT11_R__,
#elif defined(__MSP430_HAS_PORT11__)
    __MSP430_BASEADDRESS_PORT11__,
#else
    0xFFFF,
#endif
    0xFFFF,
#if defined(__MSP430_HAS_PORTJ_R__)
    __MSP430_BASEADDRESS_PORTJ_R__
#elif defined(__MSP430_HAS_PORTJ__)
    __MSP430_BASEADDRESS_PORTJ__
#else
    0xFFFF
#endif
};

void GPIO_setAsOutputPin(uint8_t selectedPort,
                         uint16_t selectedPins) {
    uint16_t baseAddress = GPIO_PORT_TO_BASE[selectedPort];

    #ifndef NDEBUG
    if(baseAddress == 0xFFFF)
    {
        return;
    }
    #endif

    // Shift by 8 if port is even (upper 8-bits)
    if((selectedPort & 1) ^ 1)
    {
        selectedPins <<= 8;
    }

    HWREG16(baseAddress + OFS_PASEL) &= ~selectedPins;
    HWREG16(baseAddress + OFS_PADIR) |= selectedPins;

    return;
}
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

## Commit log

2016-10-07 add external Watchdog Timer task
2016-10-15 Adding the modules schematics
    [CurrentToVoltage_Converter.SchDoc, Data_Retention.SchDoc, IMU.SchDoc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]
2016-10-19 Fix the refactored code to print the previous debug messages
    [debug_task.c, obdh.c, obdh_hal.h]
2016-10-21 organizing the schematics each module in numbered order
    [0_Architecture.SchDoc, 1_Interface.SchDoc, 2_Topology.SchDoc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]
2016-10-21 reformating current sensing
    [7_Current_Sensing.SchDoc]
2016-10-24 inserting new formated sheet label
    [0_Architecture.SchDoc]
2016-10-26 Adding SPI to Gyro and Temp, and current sensing
2016-10-26 updating the architecture sch
    [0_Architecture.SchDoc]
2016-10-26 first verion of interface sch
    [1_Interface.SchDoc]
2016-10-26 first version of topology sch
    [2_Topology.SchDoc]
2016-10-26 first version of MCU main adding WDT circuit
    [3_MCU_Main.SchDoc]
2016-10-28 First Revision off all OBDH sch(Matheus and Mario),
    [0_Architecture.SchDoc, 1_Interface.SchDoc, 2_Topology.SchDoc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]
2016-11-01 updating harness conections
    [0_Architecture.SchDoc, 1_Interface.SchDoc, 2_Topology.SchDoc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]
2016-11-04 finish review of OBDH sch
    [0_Architecture.SchDoc, 1_Interface.SchDoc, 2_Topology.SchDoc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]
2016-11-07 Use the XT1 crystal as sysclock to execute scaffold tasks in addition to watchdog timer task
2016-11-09 Changed WDT pins on mains MCU
    WDI -> pin 72
    MR -> pin 75
    [3_MCU_Main.SchDoc]
2016-11-10 adding the pdf of the HW
    [1_Interface.SchDoc, 3_MCU_Main.SchDoc, 6_Magnetorquer_Drivers.SchDoc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]
2016-11-24 Add IMU read feature
2016-11-30 add 3d images of obdh v2 pcb
2016-11-30 updating sch files adding the uCBeacon connections
    [1_Interface.SchDoc, 2_Topology.SchDoc, 3_MCU_Main.SchDoc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]
2016-12-09 Fixing swaped i2c interfaces
2017-01-31 Fix HAL to eng model v2
    [adc.c, clocks.c, communications_task.h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]
2017-02-17 BOM, updating sch and pdf files
    [0_Architecture.SchDoc, 1_Interface.SchDoc, 2_Topology.SchDoc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]
2017-03-02 enable to get just usefull sensor data of storage
2017-03-13 Add a folder with code to test the HW v2.1 soldering procedure
2017-03-15 Solved issue #50 and add a basic boot information
    [adc.c, clocks.c, debug_task.c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]
2017-03-22 Solved issue #64: clocks has a longer delay to startup
    [clocks.c]
2017-03-22 Update the voltage measure to the HW 2.1circuit. Solved issue #47
    [msp_internal.c, msp_internal.h]
2017-03-22 Update the gain and resistence value of current sensing circuit to agree with HW v2.1. Refers to issue #36
    [msp_internal.h]
2017-03-22 Send internal sensor data through a queue to store data task. Solve issue #46
2017-03-22 Add IMU self test. Solve issue #55
    [imu.c, imu.h]
2017-03-29 Add a command interpreter. Solve issue #21.
    [debug_task.c, floripasat_def.h]
2017-04-04 Fix a previous commit to solve issues #23 and #27
    [imu.c, imu.h]
2017-04-05 Set the internal digital oscilator(DCO) of MSP @16MHz. Issue #67
    [clocks.c]
2017-04-06 Add a set_v_core function. Will be used to analyse the issue #65
    [clocks.c, obdh_hal.h]
2017-05-02 Fix some features of I2C, as defined in issue #75
    [clocks.c, eps.c, floripasat_def.h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]
2017-05-03 include SPI driver (#37, #38, #39, #40, #41) and a non-volatile memories interface
2017-05-04 Grants a I2C reset, before starting communication
    [i2c.c, obdh_hal.h]
2017-05-05 Count the resets and save with the reset cause on flash (#77)
    [msp_internal.c, msp_internal.h, obdh.c]
2017-05-12 Change i2c functions to return timeout information (#87)
2017-05-15 Fix unimplemented verification on eps and imu status (#88)
2017-06-01 Add a mutex to protect the i2c0 interface (#93).
2017-06-05 Add Payload 1 protocol and adapt the i2c drive to this purpouse
2017-06-06 Fix the RUSH I2C slave address (#72).
    [obdh_hal.h]
2017-06-21 Add a SPI via software (#98).
2017-06-22 Implements Hibernation feature over 45 minutes after power on (#25).
2017-07-24 Include copyright and fix documentation (#101).
    [adc.c, clocks.c, communications_task.h]
2017-07-26 Change the IMU reading to 2 sampling per second (#103).
2017-08-22 Add the code to deals with the antenna deployment system. (#26, #29).
2017-08-28 Implements the antenna deployment sequence (#29).
2017-09-11 Include a Mutex when using SPI 1
2017-09-12 Store the antennas deployment status on flash (#104).
2017-09-20 Take some functions of antenna.c/.h files and put into isis_antenna.c/.h files, as a driver (#107).
2017-11-20 Fix the code to communicate with EPS using FSP (#112).
    [floripasat_def.h, obdh.c]
2017-11-21 Fix the code that communicates with TT&C using FSP (#112)
    [obdh.c]
2017-11-29 Fix tasks priorities and add mutex to flash and antenna
    [communications_task.h, debug_task.c, floripasat_def.h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]
2017-12-20 Fix tasks and add update images (#113).
    [clocks.c, communications_task.h, floripasat_def.h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]
2018-01-23 Add images for the obdh wiki
    Add some connectors images for documentation
2018-01-26 Add software flowcharts for documentation
2018-01-31 Add tasks flowcharts
2018-02-07 Update the hw topology and sw flowchart images
2018-02-15 Added magnetometer code
2018-02-19 Add a flowchart explaining how to retrieve data from memory
2018-02-27 Refactor the data frame structure to agree with specifications (#106).
    https://github.com/floripasat/obdh/wiki/Software#packets-storage-scheme
2018-04-12 Added files to calibration accelerometer
2018-04-25 Add time trace to all telecommand transmissions
2018-04-25 Fix the packet order for correct interpretation in the ground station
    [floripasat_def.h]
2018-05-15 Add verification before tasks delay to prevent wrong execution
    If a task stuck the code and the current time pass the delay of other task, this verification update the last_wake_time to prevent various inappropriate executions.
    [debug_task.c]
2018-05-16 Enable the radio interrupts in the config file and change some delays
    Same modifications as the "Fix sequencial ping telecommands reception bug", this commit sync master-dev.
2018-05-16 Add the battery charge reset telecommand handler
    [communications_task.h, eps.c, floripasat_def.h]
2018-05-21 Change the queue used to a dedicated one and fix a I2C parameter
    The previous queue is already used to make data communications. So, it is being overused and presenting an incorrect data transmission.
    [eps.c, obdh.c]
2018-05-21 Add a check if the charge reset command was correctly received in EPS
    Add a check and resend the command (up to a maximum of 3 times) if the EPS don't answer with a ACK.
    [eps.c]
2018-06-09 Fix the reset charge command tx and rx buffers
    [eps.c]
2018-06-30 Fix the telecommand counter storage
    [obdh.c]
2018-07-03 Simplify the communication with EPS to prevent I²C overhead
    [eps.c]
2018-07-17 Fix external watchdog timer toggle
2018-07-18 Fix get last write pointer function
    Removed prototype comment functions
2018-07-23 Update the XO tune register value in the RF4463 driver
2018-08-03 Add prevention default values to the energy level and the operation mode
    [msp_internal.c]
2019-02-26 add modifications
    [0_Architecture.SchDoc]
2019-05-07 Removing the IMU2 data from the telemetry packets
2019-05-14 update radio frequence and fix bug in payload_write function
    [floripasat_def.h, obdh_hal.h]
2019-05-15 Add debug routines and fix some delays
    [obdh.c]
2019-05-15 Change the RUSH interaction mode
    Add the final RUSH dynamics, fix some data addresses, comment the functions and refactor the code.
    [floripasat_def.h, payload_rush.c]
2019-05-15 Fix rush data acquisition
    [floripasat_def.h]
2019-05-24 Updating the charge reset telecommand to the new format #121
2019-07-04 Adding a routine to reset the non-volatile memory during the boot #122
    [config.h, main.c, obdh.c]
2019-07-25 Adding debug messages to the boot sequence and fixing the Doxygen documentation
    [adc.c, i2c.c, msp_internal.c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]
2019-07-27 Driver: UART: Fixing the clock configuration with a baudrate of 115200 bps
    [uart.c]
2019-07-28 Adding debug messages to the IMU and ISIS antenna interface
2019-07-29 Adding debug messages to the IMU and RUSH interfaces
2019-09-11 fix i2c leght bug
    [obdh.c]
2019-09-17 Firmware: Tasks: Disabling the IMU task
2019-09-18 fix warnings and compilations problem after merge
    [communications_task.h, floripasat_def.h, obdh.c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]
2019-09-23 Firmware: Fixing the deployment hibernation
    [obdh.c]
2019-09-27 Firmware: Fixing the merge of the "feature/paylod_x" branch
    [communications_task.h, obdh.c]
2019-09-28 correction of a error problem in a pointer and added a power up and down in payload_task
    [payload_brave.c, payload_brave.h]
2019-09-29 Firmware: Printing the antenna module temperature during the initialization

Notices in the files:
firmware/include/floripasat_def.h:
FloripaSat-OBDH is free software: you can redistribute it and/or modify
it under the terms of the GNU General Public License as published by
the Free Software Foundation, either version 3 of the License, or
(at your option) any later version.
